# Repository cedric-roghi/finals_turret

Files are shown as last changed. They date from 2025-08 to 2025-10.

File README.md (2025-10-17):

# finals_turret
A project for the hardware and software of a simple turret replica from the greatest game show on earth, The Finals.

## Table of Contents
- [Requirements](#requirements)
- [Rationale](#rationale)
- [Installation](#installation)
- [Usage](#usage)
- [Features](#features)
- [Future_Additions](#future_additions)
- [Configuration](#configuration)
- [Known_Issues](#known_issues)

## Requirements
- Software:
    - Freecad (for 3D part design)
    - KICAD (PCB design)
    - ST Cube IDE (ST account required for download)
- Hardware:
    - BOM to come
    - Access to a 3D printer

## Rationale
- STM32f411:
    - This is a pretty overkill MCU for a project such as this. It even features I2S protocol which would make it possible for me to replace the dfplayer mini module with my own custom on board audio amplifier. The whole reason to go with this 100MHz MCU is because I want to use it for a drone project so I am testing if it works as expected first with this project. It also makes things faster for the drone project if I can copy and paste the schematic.

## Installation
No code to show yet.

Current Turret design is not great and I should have designed it in pieces to be assembled. Too much support material is needed and its hard to remove without breaking the parts.

Here is the original model from the finals that the project is based on.
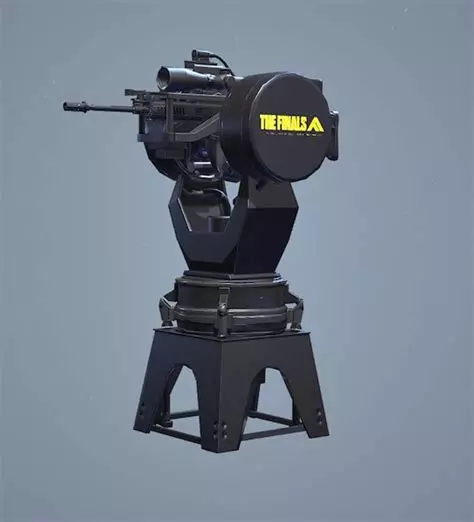
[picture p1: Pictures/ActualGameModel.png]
Game Model Its Designed After


And here is my design made in Freecad.
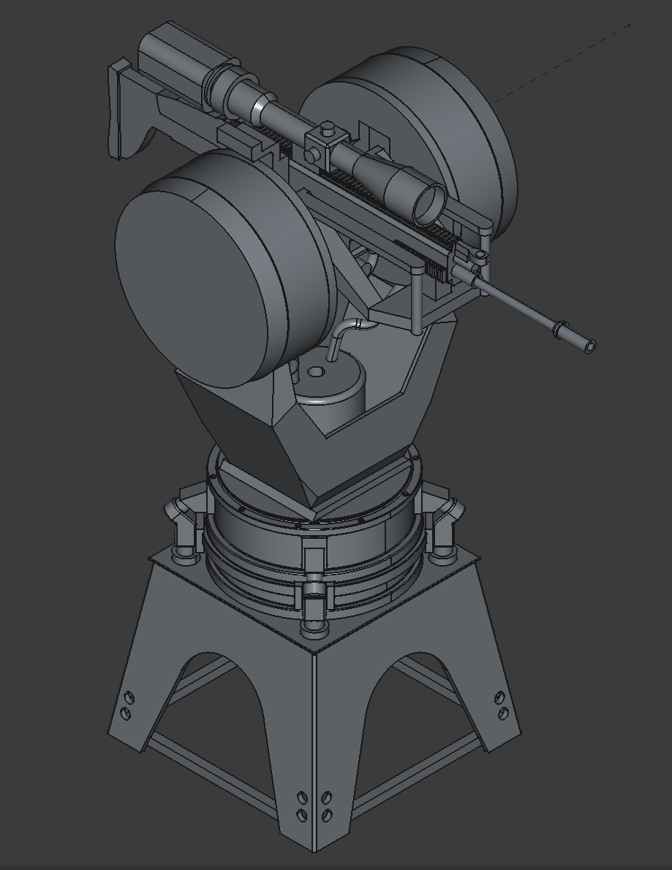
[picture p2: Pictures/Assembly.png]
Turret Assembly


Its not yet optimized for 3D printing but I believe its possible to make small changes to reduce the amount of support without affecting the looks.

FInally here is the brains of the project.
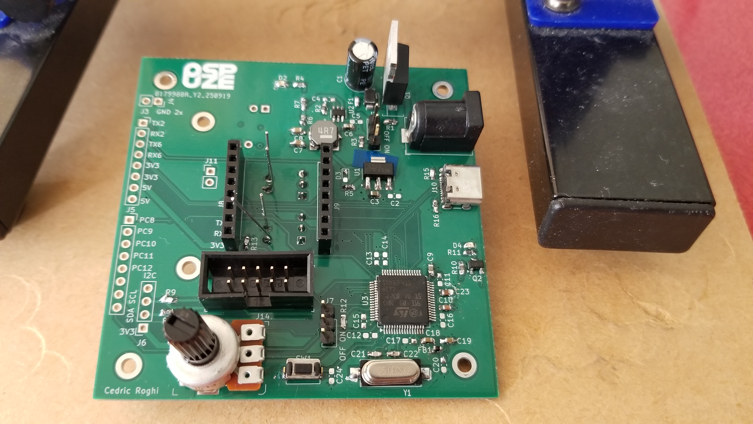
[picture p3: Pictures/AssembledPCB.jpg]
PCB


I assembled this PCB by hand using a soldering iron but I would recommend using assembly services from a manufacturer like JLCPCB. Dont forget to use a generous amount of flux if soldering the stm32 by hand.

This is how the PCB should fit into the turret. The whole thing uses M2.5 5mm screws for the speaker mounting and PCB mounting.
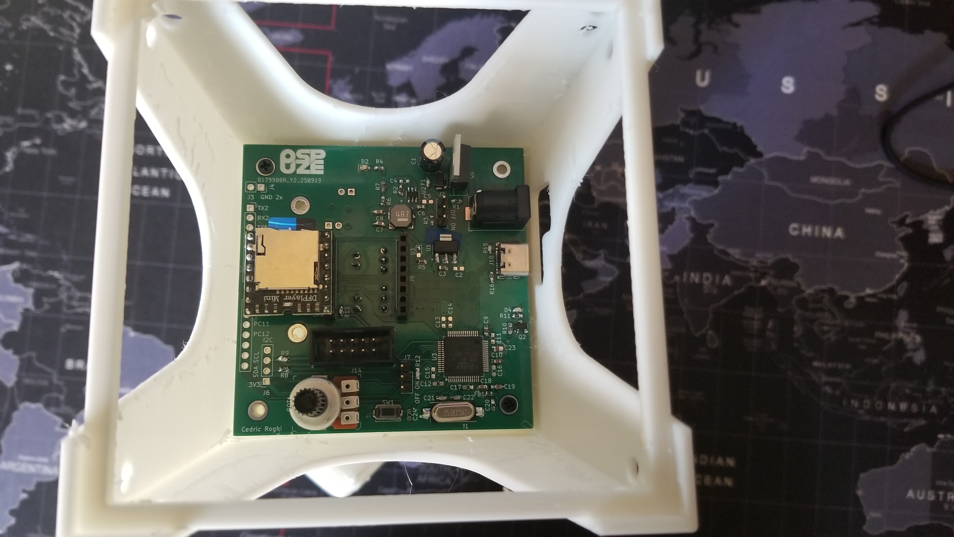
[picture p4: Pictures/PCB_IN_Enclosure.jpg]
PCB in enclosure


The servos mounting positions have mounting holes that should work with the self tapping mounting screws that are usually provided with 9g servos. The servo should be oriented so that the output rotation is in the same axis as the center of rotation for the pan and tilt respectively.

## Usage

## Features
- Audio playback using a dfplayer mini
- Programmable using SWD or USB
- USB serial communications for debugging or remote control
- USB C (2.0)
- Power input 5-12V (can use a normal 12V router power cable)
- Reverse polarity protection
- Buck converter from input stepped down to 5V for efficiency.
- Two PWM output ports to control servo motors.
- Lots of extra exposed MCU pins for rework or future quick additions.
- Potentiometer for volume control

## Future_Additions
- Raspberry pi python code for tracking people with a camera
- New and improved PCB with its own on board audio amplifier + SD card slot or some other form of audio storage

## Configuration

## Known Issues
- The standoff for the dfplayer mini is the wrong way around.
- The port for the USB and barrel jack connector should be at the back and not the side.
- The 3.3V LDO large pin is in fact connected to Vout and not GND. I need to fix the footprint in KiCAD.

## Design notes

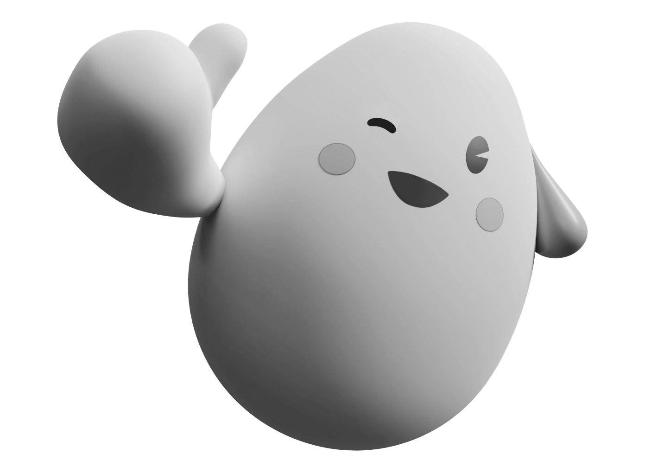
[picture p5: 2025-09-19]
Pictures/namatamagreyscale.png

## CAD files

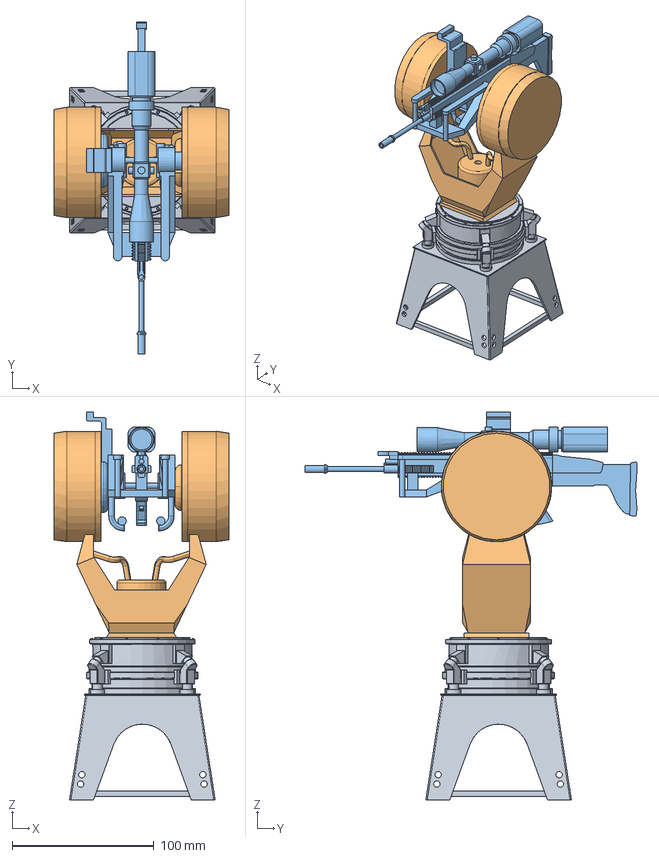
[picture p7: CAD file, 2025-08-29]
3D Assembly/TheFinalsTurretAssembly.FCStd
123.5 x 234.9 x 274.2 mm
FinalsTurretBase_V2_001
FinalsTurretTop_001
turretShooter_001
Servo TowerPro 9g SG90
Servo TowerPro 9g SG091

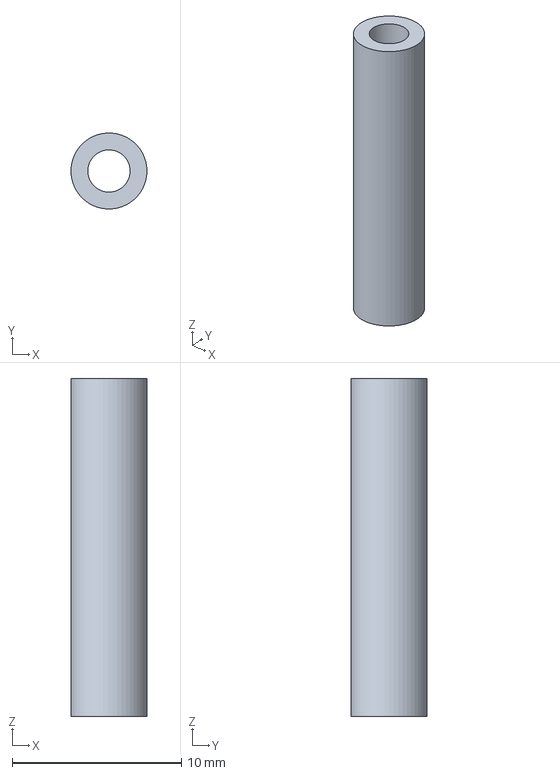
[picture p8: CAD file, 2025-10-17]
3D Assembly/SpeakerStandoffs.FCStd
4.50 x 4.50 x 20.0 mm

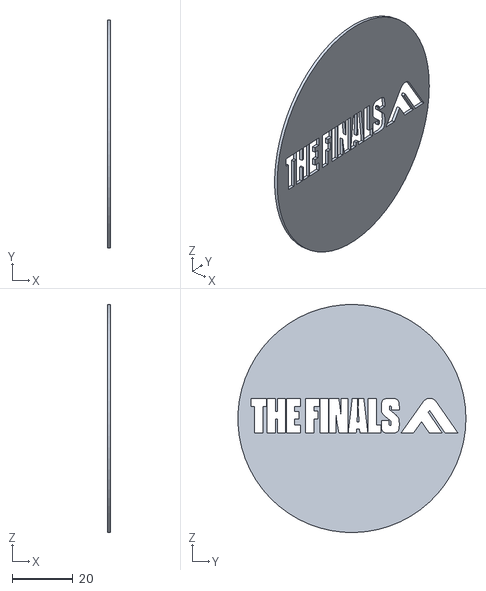
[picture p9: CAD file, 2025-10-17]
3D Assembly/STL_FILES/FinalsTurretTop-LogoStencil.stl
1.00 x 75.3 x 75.3

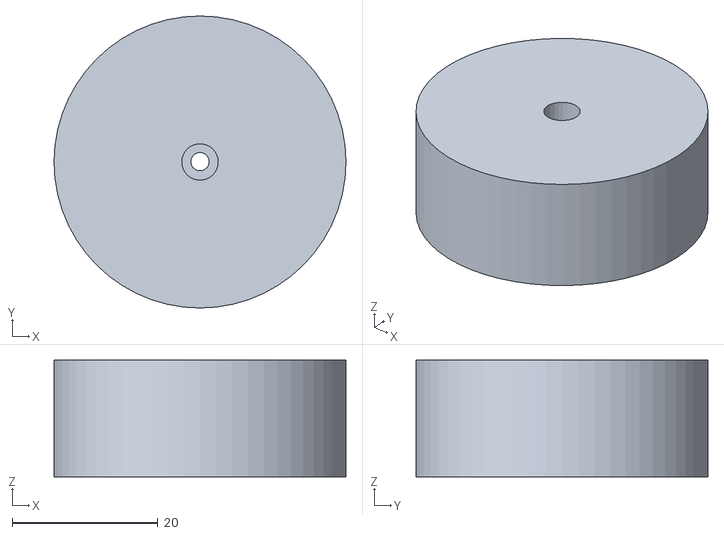
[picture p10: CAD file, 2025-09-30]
3D Assembly/STL_FILES/FinalsTurretTop-ServoArmFitTest.stl
40.0 x 40.0 x 16.0

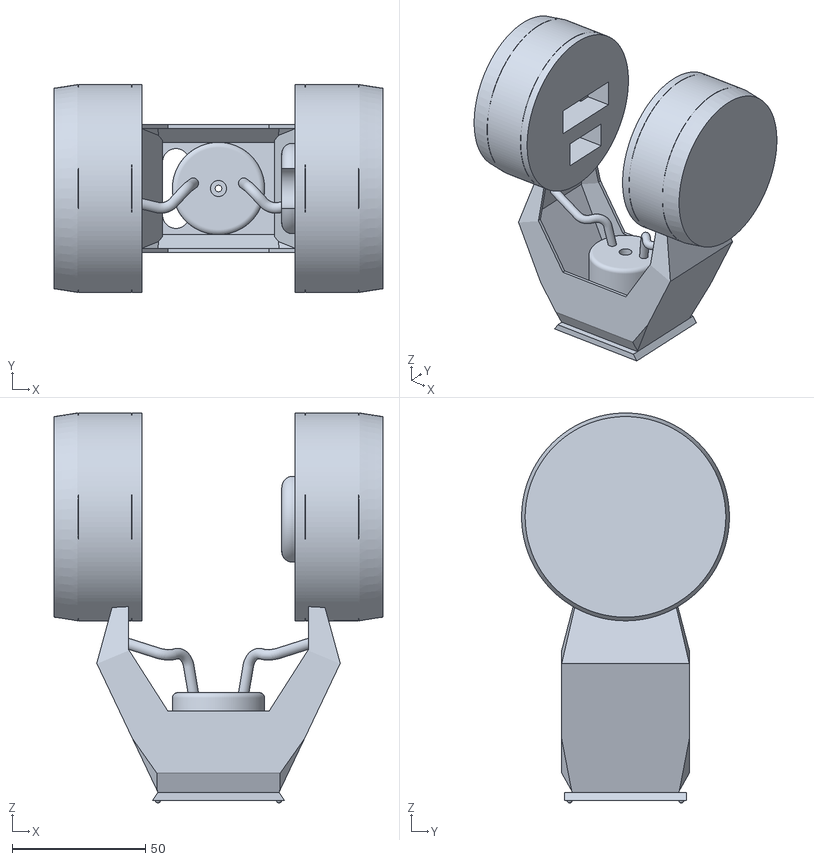
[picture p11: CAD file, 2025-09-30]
3D Assembly/STL_FILES/FinalsTurretTop-Body.stl
123.5 x 78.1 x 146.6

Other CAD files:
3D Assembly/STL_FILES/SpeakerStandoffs-Body.stl

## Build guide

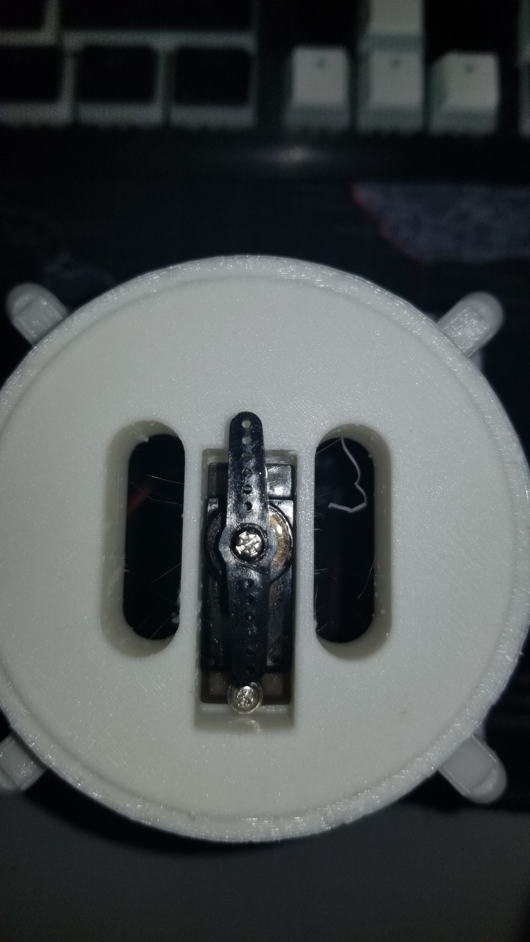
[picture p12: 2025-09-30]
3D Assembly/servoarmreference.jpg

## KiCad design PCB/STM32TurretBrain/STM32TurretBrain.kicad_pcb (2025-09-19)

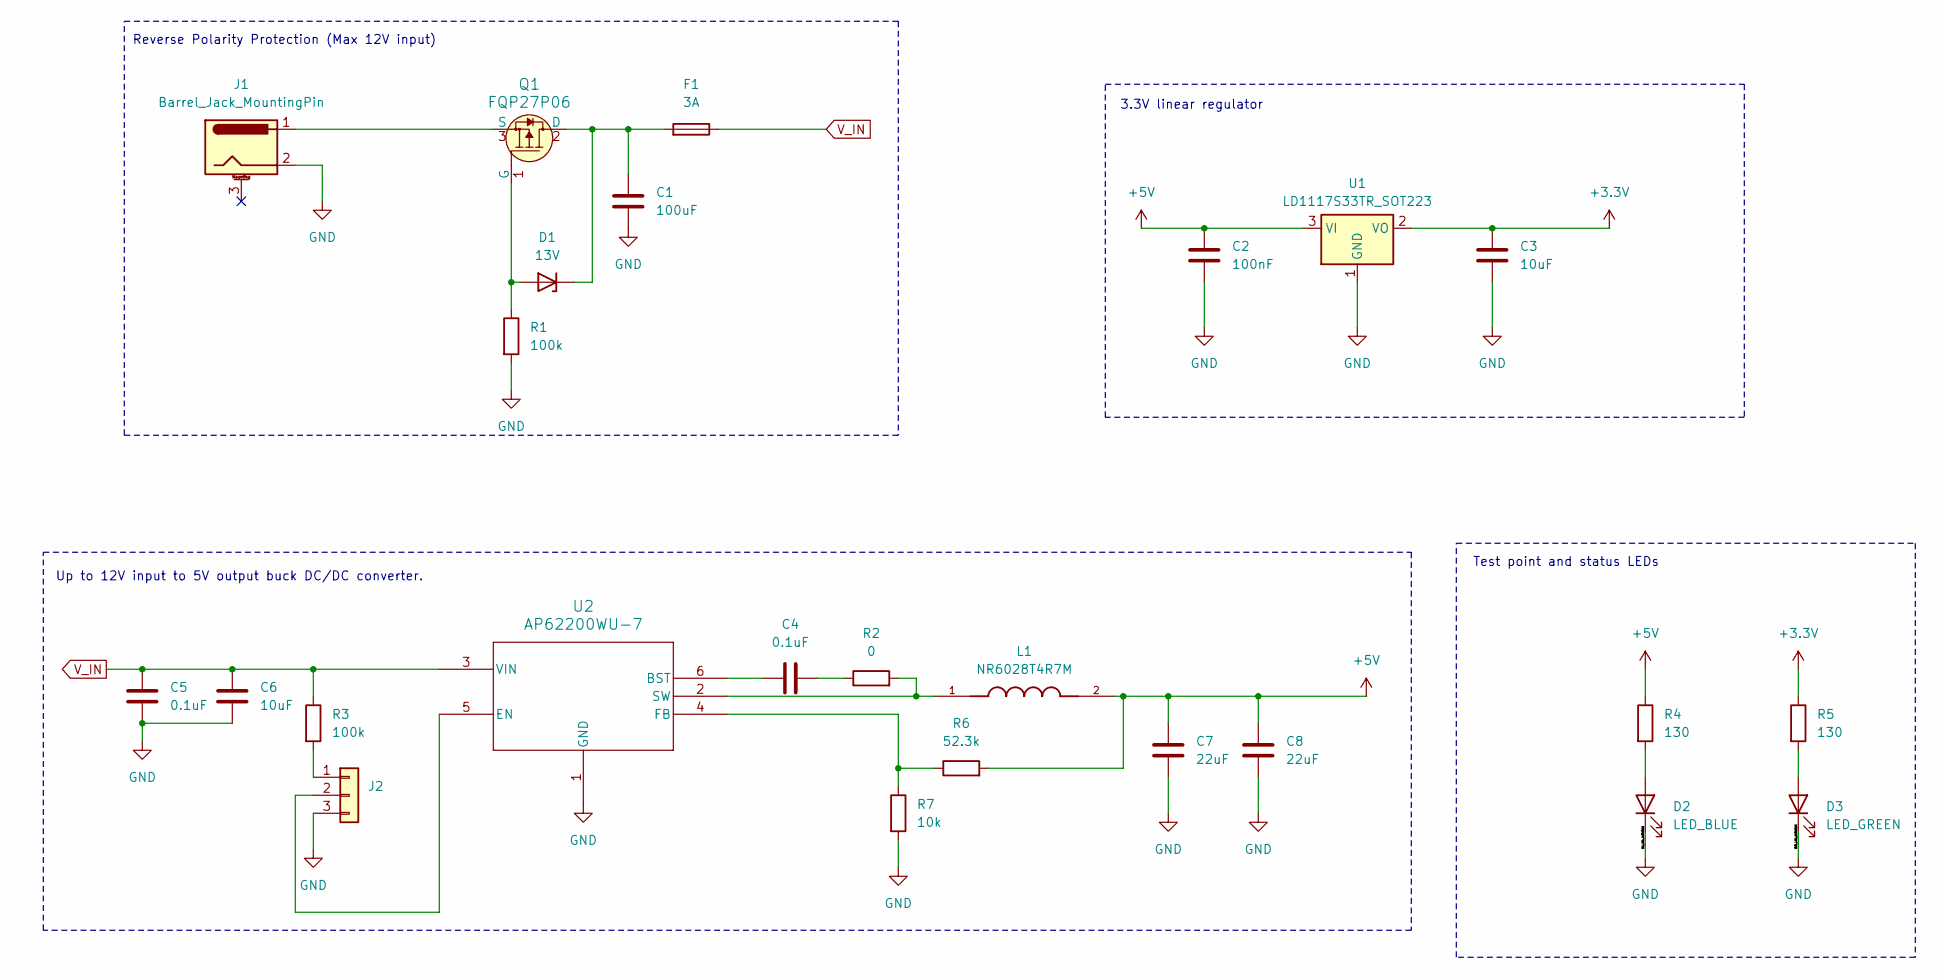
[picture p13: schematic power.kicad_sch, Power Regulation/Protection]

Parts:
C1: 100uF; C_Radial_D6.3mm_H5.0mm_P2.50mm
C2: 100nF; C_0603_1608Metric_Pad1.08x0.95mm_HandSolder
C3, C6: 10uF; C_0603_1608Metric_Pad1.08x0.95mm_HandSolder
C4, C5: 0.1uF; C_0603_1608Metric_Pad1.08x0.95mm_HandSolder
C7, C8: 22uF; C_0603_1608Metric_Pad1.08x0.95mm_HandSolder
D1: 13V; Nexperia_CFP3_SOD-123W
D2: LED_BLUE; LED_0603_1608Metric_Pad1.05x0.95mm_HandSolder
D3: LED_GREEN; LED_0603_1608Metric_Pad1.05x0.95mm_HandSolder
F1: 3A; Fuse_0603_1608Metric_Pad1.05x0.95mm_HandSolder
J1: Barrel_Jack_MountingPin; BarrelJack_Horizontal
J2: Conn_01x03; PinHeader_1x03_P2.54mm_Vertical
L1: NR6028T4R7M; IND_NR6028T4R7M
Q1: FQP27P06; TO-220-3; MPN FQP27P06; Digi-Key_PN FQP27P06-ND
R1, R3: 100k; R_0603_1608Metric_Pad0.98x0.95mm_HandSolder
R2: 0; R_0603_1608Metric_Pad0.98x0.95mm_HandSolder
R4, R5: 130; R_0603_1608Metric_Pad0.98x0.95mm_HandSolder
R6: 52.3k; R_0603_1608Metric_Pad0.98x0.95mm_HandSolder
R7: 10k; R_0603_1608Metric_Pad0.98x0.95mm_HandSolder
U1: LD1117S33TR_SOT223; SOT-223
U2: AP62200WU-7; TSOT26-WU_DIO-M

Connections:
+3.3V: C3.1, R5.1, U1.2 (VO); also elsewhere on the board
+5V: C2.1, C7.1, C8.1, L1.2, R4.1, R6.2, U1.3 (VI); also elsewhere on the board
GND: C1.2, C2.2, C3.2, C5.2, C6.2, C7.2, C8.2, D2.1 (K), D3.1 (K), J1.2, J2.3, R1.2, R7.2, U1.1 (GND), U2.1 (GND); also elsewhere on the board
unnamed: C4.2, R2.1
unnamed: D1.2 (A), Q1.1 (G), R1.1
unnamed: C1.1, D1.1 (K), F1.2, Q1.2 (D)
unnamed: D2.2 (A), R4.2
unnamed: D3.2 (A), R5.2
unnamed: J2.1, R3.2
unnamed: J2.2, U2.5 (EN)
unnamed: J1.1, Q1.3 (S)
unnamed: C4.1, U2.6 (BST)
unnamed: R6.1, R7.1, U2.4 (FB)
unnamed: L1.1, R2.2, U2.2 (SW)
V_IN: C5.1, C6.1, F1.1, R3.1, U2.3 (VIN)

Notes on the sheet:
Up to 12V input to 5V output buck DC/DC converter.
3.3V linear regulator
Test point and status LEDs
Reverse Polarity Protection (Max 12V input)

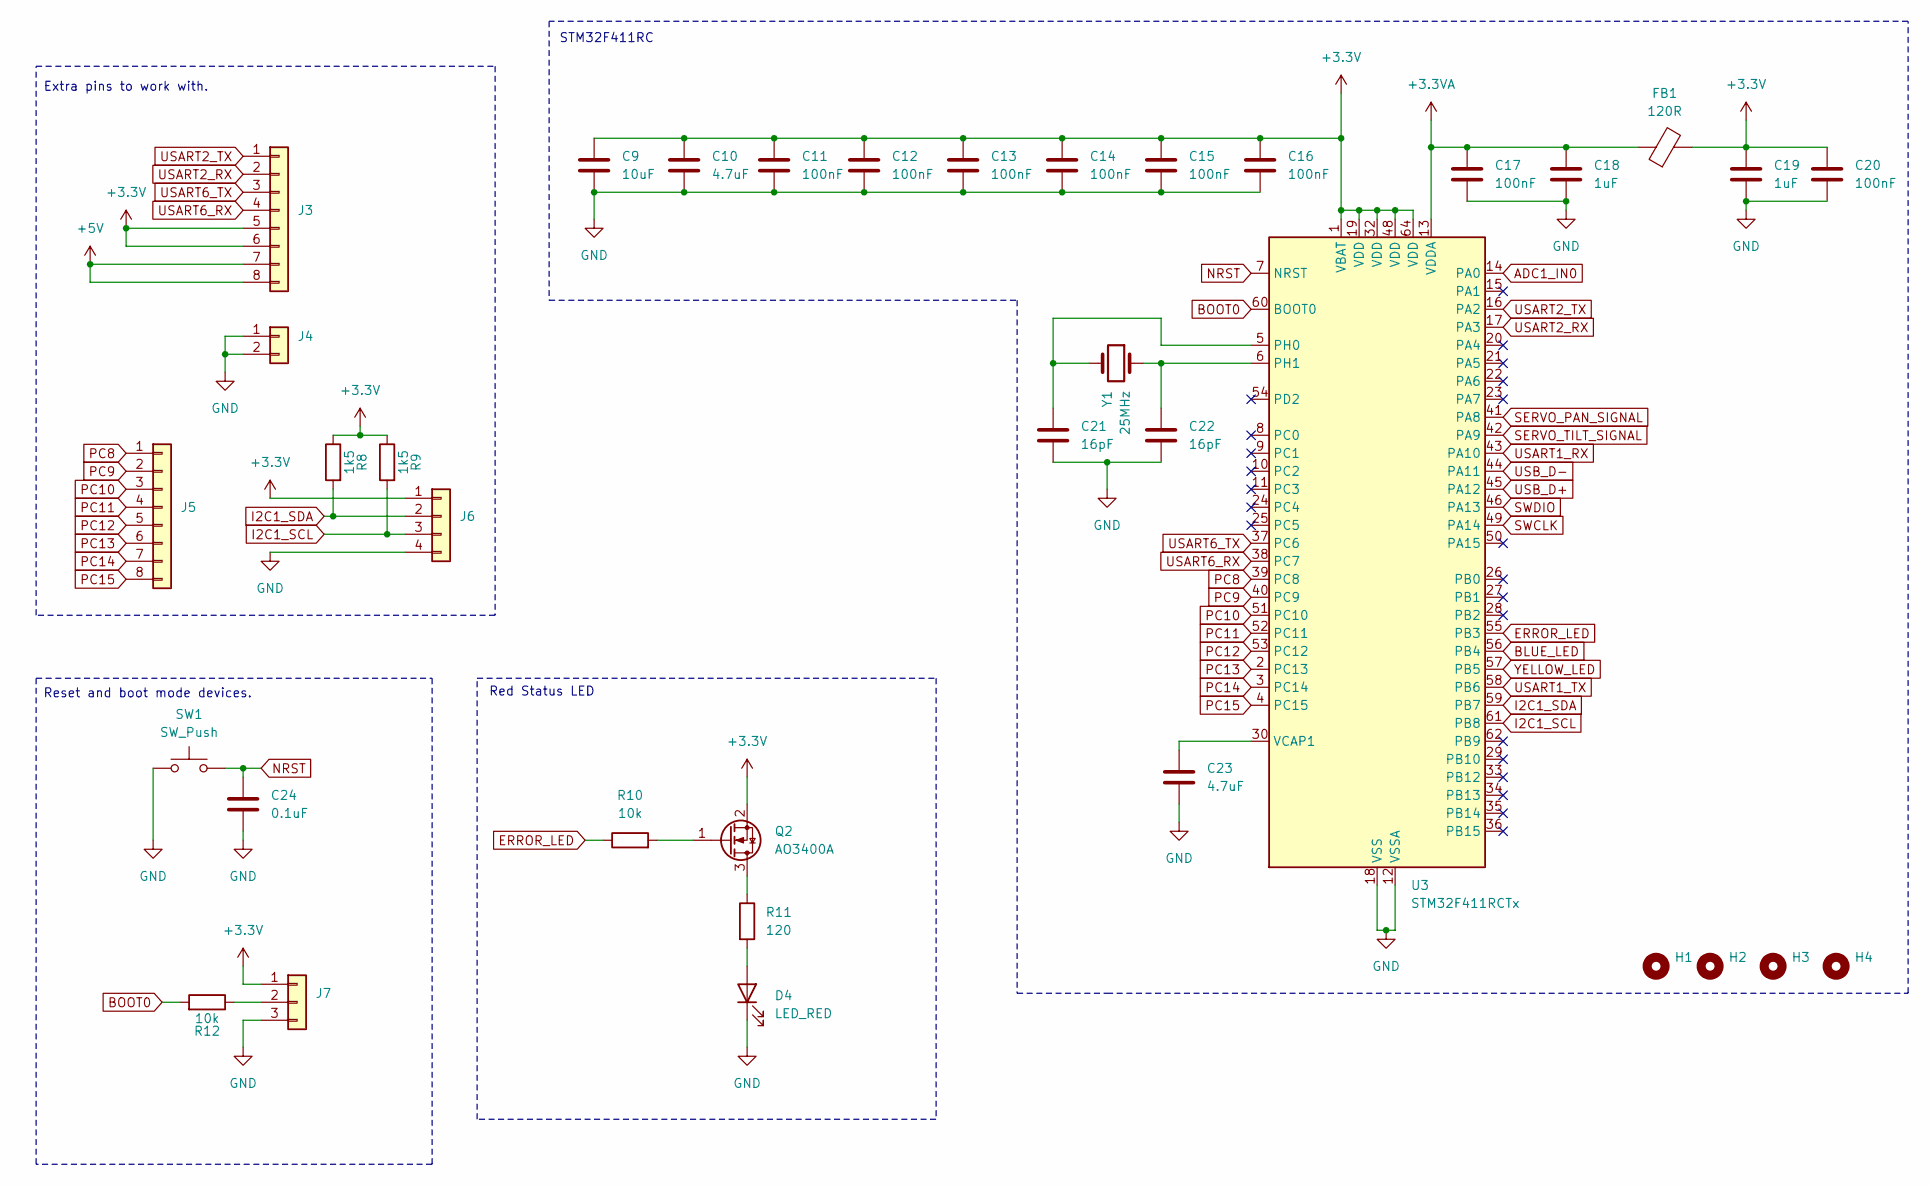
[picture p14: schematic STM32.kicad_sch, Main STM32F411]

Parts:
C9: 10uF; C_0603_1608Metric_Pad1.08x0.95mm_HandSolder
C10, C23: 4.7uF; C_0603_1608Metric_Pad1.08x0.95mm_HandSolder
C11, C12, C13, C14, C15, C16, C17, C20: 100nF; C_0603_1608Metric_Pad1.08x0.95mm_HandSolder
C18, C19: 1uF; C_0603_1608Metric_Pad1.08x0.95mm_HandSolder
C21, C22: 16pF; C_0603_1608Metric_Pad1.08x0.95mm_HandSolder
C24: 0.1uF; C_0603_1608Metric_Pad1.08x0.95mm_HandSolder
D4: LED_RED; LED_0603
FB1: 120R; 0603
H1, H2, H3, H4: MountingHole; MountingHole_2.7mm_M2.5_DIN965_Pad
J3, J5: Conn_01x08; PinSocket_1x08_P2.54mm_Vertical
J4: Conn_01x02; PinSocket_1x02_P2.54mm_Vertical
J6: Conn_01x04; PinSocket_1x04_P2.54mm_Vertical
J7: Conn_01x03; PinHeader_1x03_P2.54mm_Vertical
Q2: AO3400A; SOT-23
R8, R9: 1k5; R_0603_1608Metric_Pad0.98x0.95mm_HandSolder
R10, R12: 10k; R_0603_1608Metric_Pad0.98x0.95mm_HandSolder
R11: 120; R_0603_1608Metric_Pad0.98x0.95mm_HandSolder
SW1: SW_Push; SW_SPST_EVQPE1
U3: STM32F411RCTx; LQFP-64_10x10mm_P0.5mm
Y1: 25MHz; XTAL_ECS-250-18-5PX-F-TR

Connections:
+3.3V: C9.1, C10.1, C11.1, C12.1, C13.1, C14.1, C15.1, C16.1, C19.1, C20.1, FB1.2, J3.5, J3.6, J6.1, J7.1, Q2.2 (S), R8.1, R9.1, U3.1 (VBAT), U3.19 (VDD), U3.32 (VDD), U3.48 (VDD), U3.64 (VDD); also elsewhere on the board
+3.3VA: C17.1, C18.1, FB1.1, U3.13 (VDDA)
+5V: J3.7, J3.8; also elsewhere on the board
ADC1_IN0: U3.14 (PA0); also elsewhere on the board
BLUE_LED: U3.56 (PB4); also elsewhere on the board
BOOT0: R12.2, U3.60 (BOOT0)
ERROR_LED: R10.1, U3.55 (PB3)
GND: C9.2, C10.2, C11.2, C12.2, C13.2, C14.2, C15.2, C16.2, C17.2, C18.2, C19.2, C20.2, C21.2, C22.2, C23.2, C24.2, D4.1 (K), J4.1, J4.2, J6.4, J7.3, SW1.1, U3.12 (VSSA), U3.18 (VSS), U3.31 (VSS), U3.47 (VSS), U3.63 (VSS); also elsewhere on the board
I2C1_SCL: J6.3, R9.2, U3.61 (PB8)
I2C1_SDA: J6.2, R8.2, U3.59 (PB7)
NRST: C24.1, SW1.2, U3.7 (NRST)
unnamed: D4.2 (A), R11.2
unnamed: J7.2, R12.1
unnamed: Q2.3 (D), R11.1
unnamed: Q2.1 (G), R10.2
unnamed: C21.1, U3.5 (PH0), Y1.2
unnamed: C22.1, U3.6 (PH1), Y1.1
unnamed: C23.1, U3.30 (VCAP1)
PC8: J5.1, U3.39 (PC8)
PC9: J5.2, U3.40 (PC9)
PC10: J5.3, U3.51 (PC10)
PC11: J5.4, U3.52 (PC11)
PC12: J5.5, U3.53 (PC12)
PC13: J5.6, U3.2 (PC13)
PC14: J5.7, U3.3 (PC14)
PC15: J5.8, U3.4 (PC15)
SERVO_PAN_SIGNAL: U3.41 (PA8); also elsewhere on the board
SERVO_TILT_SIGNAL: U3.42 (PA9); also elsewhere on the board
SWCLK: U3.49 (PA14); also elsewhere on the board
SWDIO: U3.46 (PA13); also elsewhere on the board
USART1_RX: U3.43 (PA10); also elsewhere on the board
USART1_TX: U3.58 (PB6); also elsewhere on the board
USART2_RX: J3.2, U3.17 (PA3)
USART2_TX: J3.1, U3.16 (PA2)
USART6_RX: J3.4, U3.38 (PC7)
USART6_TX: J3.3, U3.37 (PC6)
USB_D+: U3.45 (PA12); also elsewhere on the board
USB_D-: U3.44 (PA11); also elsewhere on the board
YELLOW_LED: U3.57 (PB5); also elsewhere on the board

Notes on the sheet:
Extra pins to work with.
Red Status LED
STM32F411RC
Reset and boot mode devices.

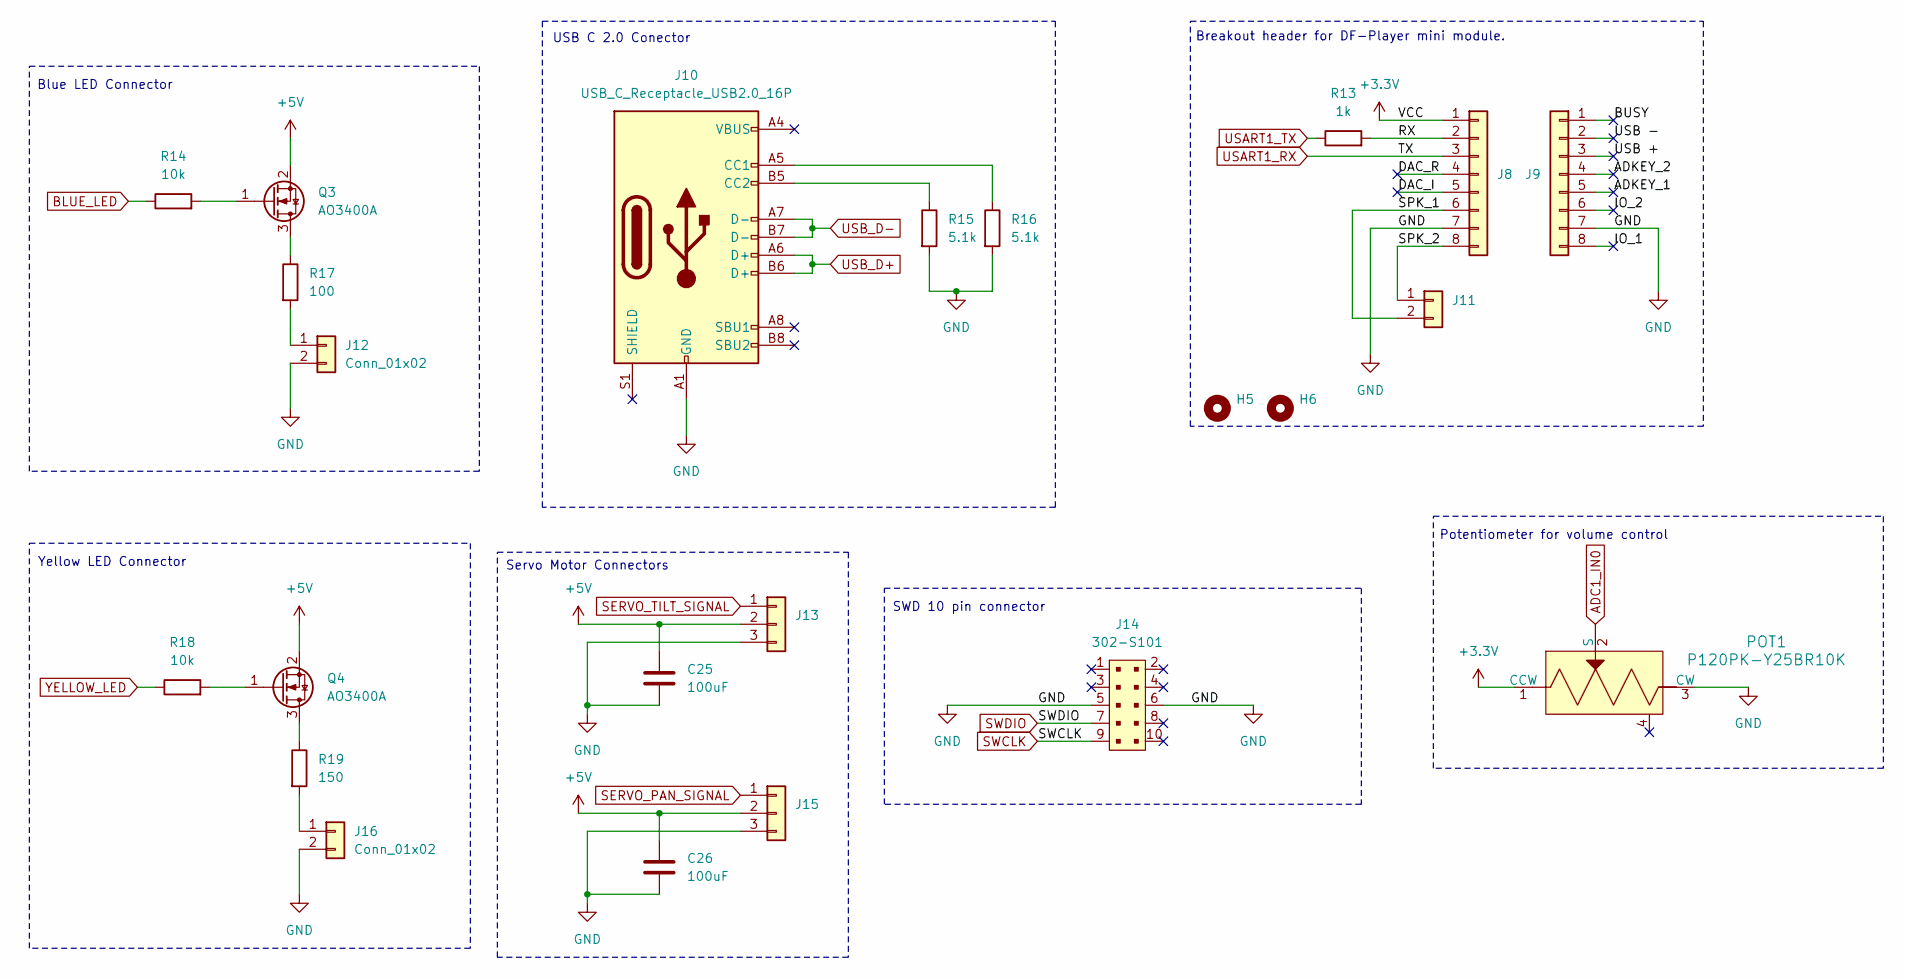
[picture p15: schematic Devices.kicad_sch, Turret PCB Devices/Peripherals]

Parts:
C25, C26: 100uF; C_Radial_D6.3mm_H5.0mm_P2.50mm
H5, H6: MountingHole; MountingHole_2.7mm_M2.5_DIN965_Pad
J8, J9: Conn_01x08; PinHeader_1x08_P2.54mm_Vertical
J10: USB_C_Receptacle_USB2.0_16P; USB_C_Receptacle_GCT_USB4105-xx-A_16P_TopMnt_Horizontal
J11: Conn_01x02; PinHeader_1x02_P2.54mm_Vertical
J12, J16: Conn_01x02; PinSocket_1x02_P2.54mm_Vertical
J13, J15: Conn_01x03; PinHeader_1x03_P2.54mm_Vertical
J14: 302-S101; PinHeader_2x5_P2.54mm_Drill1.2mm; MPN 302-S101; Digi-Key_PN ED1543-ND
POT1: P120PK-Y25BR10K; Potentiometer_P120PK-Y25BR10K; MPN P120PK-Y25BR10K; Digi-Key_PN 987-1710-ND
Q3, Q4: AO3400A; SOT-23
R13: 1k; R_0603_1608Metric_Pad0.98x0.95mm_HandSolder
R14, R18: 10k; R_0603_1608Metric_Pad0.98x0.95mm_HandSolder
R15, R16: 5.1k; R_0603_1608Metric_Pad0.98x0.95mm_HandSolder
R17: 100; R_0603_1608Metric_Pad0.98x0.95mm_HandSolder
R19: 150; R_0603_1608Metric_Pad0.98x0.95mm_HandSolder

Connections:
+3.3V: J8.1, POT1.1 (CCW); also elsewhere on the board
+5V: C25.1, C26.1, J13.2, J15.2, Q3.2 (S), Q4.2 (S); also elsewhere on the board
/Devices/ADKEY_1: J9.5
/Devices/ADKEY_2: J9.4
/Devices/BUSY: J9.1
/Devices/DAC_I: J8.5
/Devices/DAC_R: J8.4
/Devices/IO_1: J9.8
/Devices/IO_2: J9.6
/Devices/RX: J8.2, R13.2
/Devices/SPK_1: J8.6, J11.2
/Devices/SPK_2: J8.8, J11.1
/Devices/USB +: J9.3
/Devices/USB -: J9.2
ADC1_IN0: POT1.2 (S); also elsewhere on the board
BLUE_LED: R14.1; also elsewhere on the board
GND: C25.2, C26.2, J8.7, J9.7, J10.A1 (GND), J10.A12 (GND), J10.B1 (GND), J10.B12 (GND), J12.2, J13.3, J14.5, J14.6, J15.3, J16.2, POT1.3 (CW), R15.2, R16.2; also elsewhere on the board
unnamed: J10.A5 (CC1), R16.1
unnamed: J10.B5 (CC2), R15.1
unnamed: J12.1, R17.2
unnamed: J16.1, R19.2
unnamed: Q3.3 (D), R17.1
unnamed: Q3.1 (G), R14.2
unnamed: Q4.3 (D), R19.1
unnamed: Q4.1 (G), R18.2
SERVO_PAN_SIGNAL: J15.1; also elsewhere on the board
SERVO_TILT_SIGNAL: J13.1; also elsewhere on the board
SWCLK: J14.9; also elsewhere on the board
SWDIO: J14.7; also elsewhere on the board
USART1_RX: J8.3; also elsewhere on the board
USART1_TX: R13.1; also elsewhere on the board
USB_D+: J10.A6 (D+), J10.B6 (D+); also elsewhere on the board
USB_D-: J10.A7 (D-), J10.B7 (D-); also elsewhere on the board
YELLOW_LED: R18.1; also elsewhere on the board

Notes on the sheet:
Servo Motor Connectors
USB C 2.0 Conector
Blue LED Connector
Yellow LED Connector
SWD 10 pin connector
Breakout header for DF-Player mini module.
Potentiometer for volume control

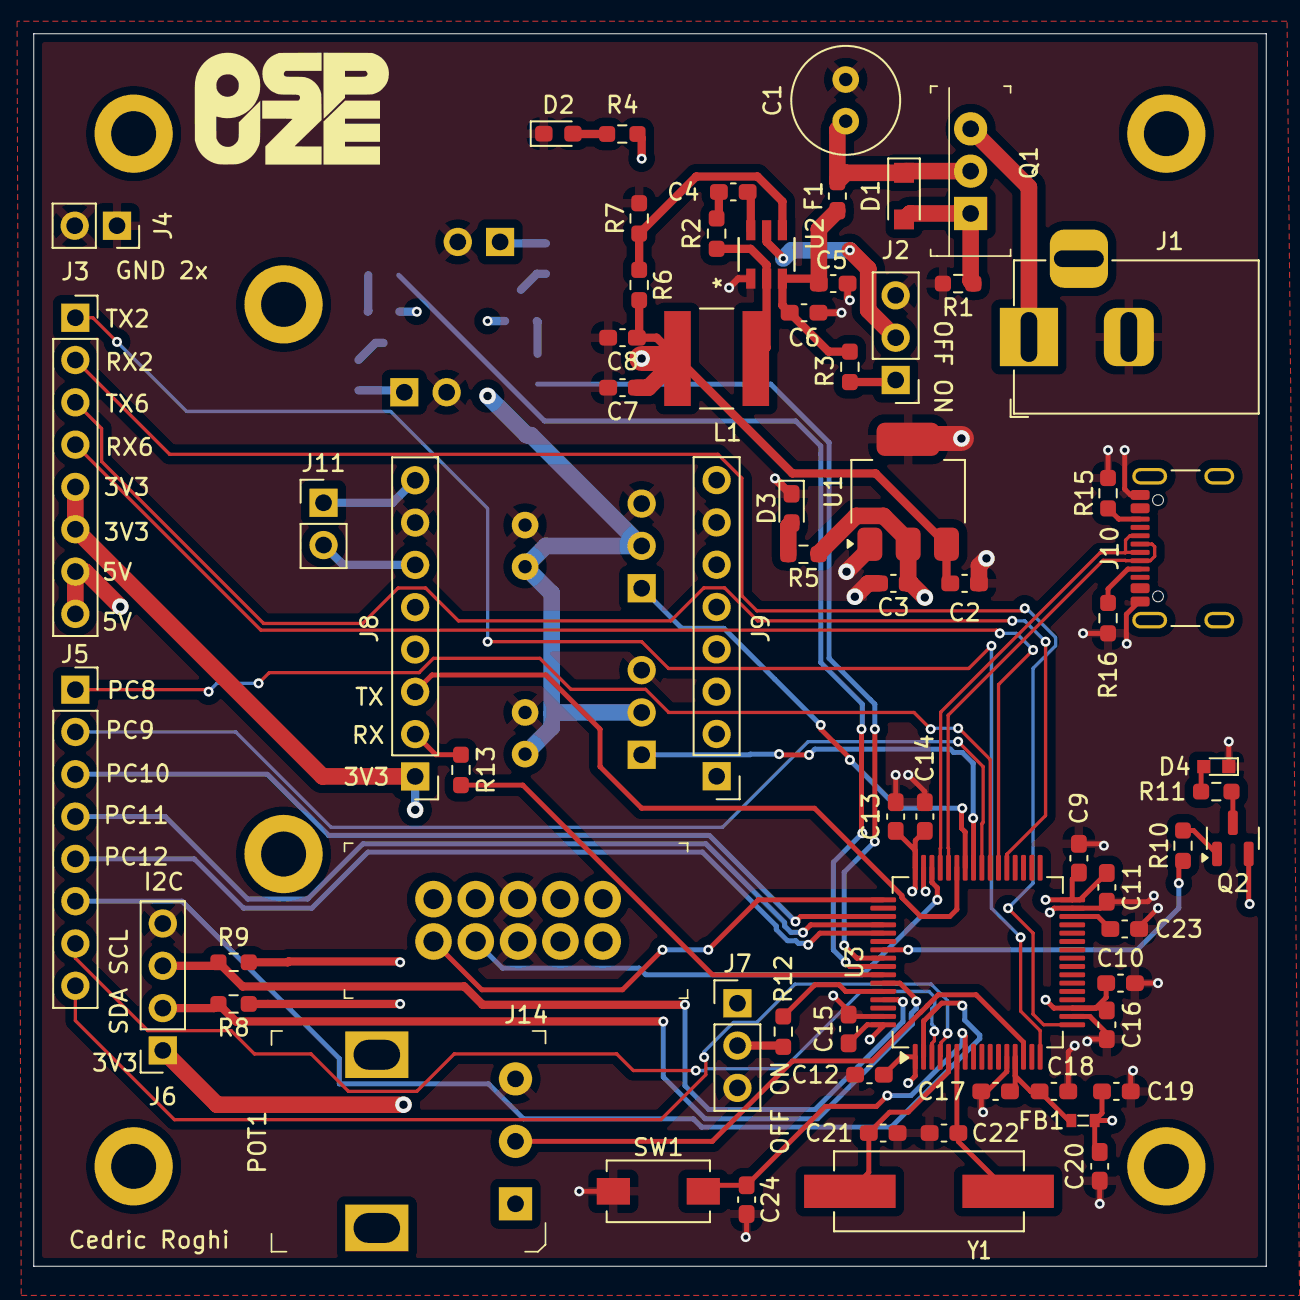
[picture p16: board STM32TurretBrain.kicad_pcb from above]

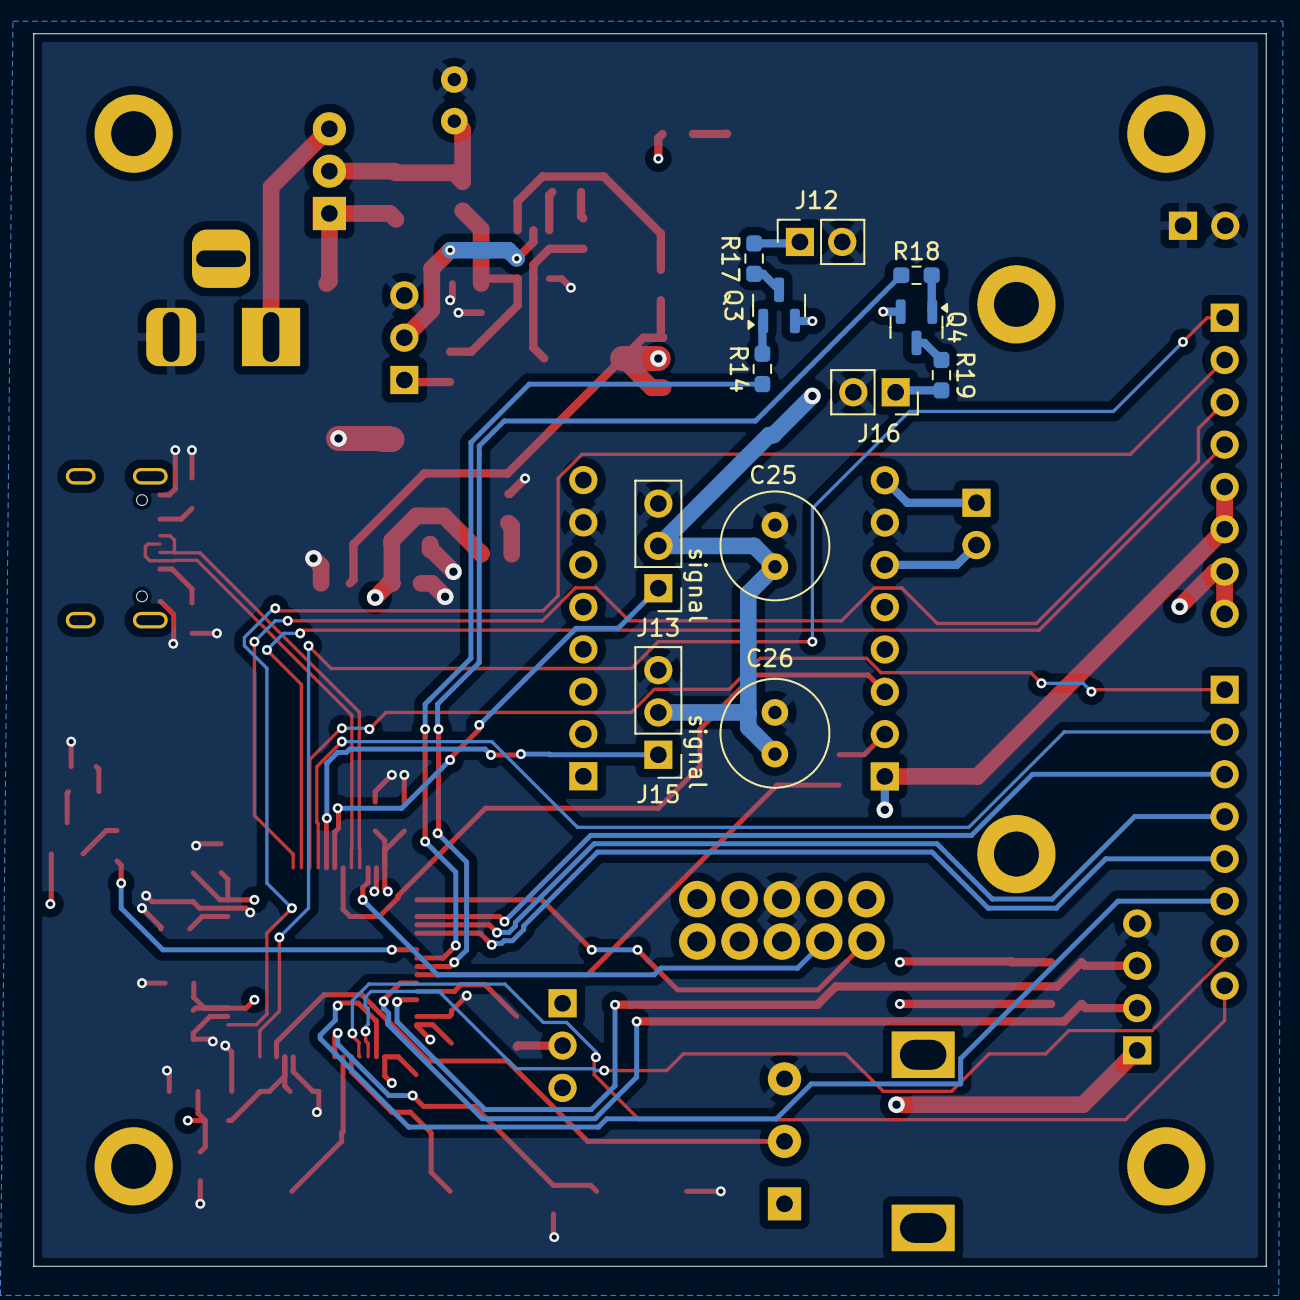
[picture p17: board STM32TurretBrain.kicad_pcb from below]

Board: 4 copper layers, 74.0 x 74.0 mm, 84 parts (12 on the bottom side), 62 nets.

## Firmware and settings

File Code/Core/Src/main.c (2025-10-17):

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
/* Includes ------------------------------------------------------------------*/
#include "main.h"
#include "cmsis_os.h"

ADC_HandleTypeDef hadc1;

TIM_HandleTypeDef htim1;

UART_HandleTypeDef huart1;

PCD_HandleTypeDef hpcd_USB_OTG_FS;

/* Definitions for defaultTask */
osThreadId_t defaultTaskHandle;
const osThreadAttr_t defaultTask_attributes = {
  .name = "defaultTask",
  .stack_size = 128 * 4,
  .priority = (osPriority_t) osPriorityNormal,
};
void SystemClock_Config(void);
static void MX_GPIO_Init(void);
static void MX_TIM1_Init(void);
static void MX_USART1_UART_Init(void);
static void MX_USB_OTG_FS_PCD_Init(void);
static void MX_ADC1_Init(void);
void StartDefaultTask(void *argument);

/**
  * @brief  The application entry point.
  * @retval int
  */
int main(void)
{

  /* MCU Configuration--------------------------------------------------------*/

  /* Reset of all peripherals, Initializes the Flash interface and the Systick. */
  HAL_Init();

  /* Configure the system clock */
  SystemClock_Config();

  /* Initialize all configured peripherals */
  MX_GPIO_Init();
  MX_TIM1_Init();
  MX_USART1_UART_Init();
  MX_USB_OTG_FS_PCD_Init();
  MX_ADC1_Init();
  /* USER CODE BEGIN 2 */
  HAL_TIM_PWM_Start(&htim1, TIM_CHANNEL_1);
  /* USER CODE END 2 */

  /* Init scheduler */
  osKernelInitialize();

  /* USER CODE BEGIN RTOS_MUTEX */
  /* add mutexes, ... */
  /* USER CODE END RTOS_MUTEX */

  /* USER CODE BEGIN RTOS_SEMAPHORES */
  /* add semaphores, ... */
  /* USER CODE END RTOS_SEMAPHORES */

  /* USER CODE BEGIN RTOS_TIMERS */
  /* start timers, add new ones, ... */
  /* USER CODE END RTOS_TIMERS */

  /* USER CODE BEGIN RTOS_QUEUES */
  /* add queues, ... */
  /* USER CODE END RTOS_QUEUES */

  /* Create the thread(s) */
  /* creation of defaultTask */
  defaultTaskHandle = osThreadNew(StartDefaultTask, NULL, &defaultTask_attributes);

  /* USER CODE BEGIN RTOS_THREADS */
  /* add threads, ... */
  /* USER CODE END RTOS_THREADS */

  /* USER CODE BEGIN RTOS_EVENTS */
  /* add events, ... */
  /* USER CODE END RTOS_EVENTS */

  /* Start scheduler */
  osKernelStart();

  /* We should never get here as control is now taken by the scheduler */

  /* Infinite loop */
  /* USER CODE BEGIN WHILE */
  while (1)
  {
    /* USER CODE END WHILE */

    /* USER CODE BEGIN 3 */
  }
  /* USER CODE END 3 */
}

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
/* USER CODE BEGIN 4 */
static uint32_t AngleToCCR(uint16_t angle)
{
    const uint32_t MIN_PULSE_US = 500;   // 1 ms
    const uint32_t MAX_PULSE_US = 2500;   // 2 ms

    if (angle > 180U) angle = 180U;        // clamp

    return MIN_PULSE_US +
           ((MAX_PULSE_US - MIN_PULSE_US) * angle) / 180U;
}

void Pan_Servo_SetAngle(uint16_t angle)
{
    __HAL_TIM_SET_COMPARE(&htim1, TIM_CHANNEL_1, AngleToCCR(angle));
}

static uint16_t ADC_Value_To_Angle(uint32_t adc_val)
{
    /* Clamp just in case */
    if (adc_val > 4095U) adc_val = 4095U;

    /* Linear mapping: 0 → 0°, 4095 → 180° */
    return (uint16_t)((adc_val * 180U) / 4095U);
}
/* USER CODE END 4 */

/* USER CODE BEGIN Header_StartDefaultTask */
/**
  * @brief  Function implementing the defaultTask thread.
  * @param  argument: Not used
  * @retval None
  */
/* USER CODE END Header_StartDefaultTask */
void StartDefaultTask(void *argument)
{
  /* USER CODE BEGIN 5 */
  /* Infinite loop */
	while (1)
	{
		uint32_t adc_raw = 0;

		/* ---- 1. Trigger a single conversion -------------------------------- */
		HAL_ADC_Start(&hadc1);                     // start conversion
		if (HAL_ADC_PollForConversion(&hadc1, 10) == HAL_OK)   // timeout = 10 ms
		{
			adc_raw = HAL_ADC_GetValue(&hadc1);    // 0 … 4095
		}
		HAL_ADC_Stop(&hadc1);                      // stop (optional, saves power)

		/* ---- 2. Convert ADC → angle --------------------------------------- */
		uint16_t angle = ADC_Value_To_Angle(adc_raw);

		/* ---- 3. Convert angle → CCR and write it --------------------------- */
		uint32_t ccr = AngleToCCR(angle);
		__HAL_TIM_SET_COMPARE(&htim1, TIM_CHANNEL_1, ccr);

		/* ---- 4. Small delay – you can tune this to taste ----------------- */
		osDelay(20);      // 20 ms ≈ one PWM period; feel free to increase
	}
  /* USER CODE END 5 */
}

/**
  * @brief  Period elapsed callback in non blocking mode
  * @note   This function is called  when TIM2 interrupt took place, inside
  * HAL_TIM_IRQHandler(). It makes a direct call to HAL_IncTick() to increment
  * a global variable "uwTick" used as application time base.
  * @param  htim : TIM handle
  * @retval None
  */
void HAL_TIM_PeriodElapsedCallback(TIM_HandleTypeDef *htim)
{
  if (htim->Instance == TIM2)
  {
    HAL_IncTick();
  }
}

/**
  * @brief  This function is executed in case of error occurrence.
  * @retval None
  */
void Error_Handler(void)
{
  /* USER CODE BEGIN Error_Handler_Debug */
  /* User can add his own implementation to report the HAL error return state */
  __disable_irq();
  while (1)
  {
  }
  /* USER CODE END Error_Handler_Debug */
}
#ifdef USE_FULL_ASSERT
/**
  * @brief  Reports the name of the source file and the source line number
  *         where the assert_param error has occurred.
  * @param  file: pointer to the source file name
  * @param  line: assert_param error line source number
  * @retval None
  */
void assert_failed(uint8_t *file, uint32_t line)
{
  /* USER CODE BEGIN 6 */
  /* User can add his own implementation to report the file name and line number,
     ex: printf("Wrong parameters value: file %s on line %d\r\n", file, line) */
  /* USER CODE END 6 */
}
#endif /* USE_FULL_ASSERT */

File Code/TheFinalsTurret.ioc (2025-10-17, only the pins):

Mcu.UserName=STM32F411RCTx
PA0-WKUP.Signal=ADCx_IN0
PA10.Signal=USART1_RX
PA11.Signal=USB_OTG_FS_DM
PA12.Signal=USB_OTG_FS_DP
PA13.Signal=SYS_JTMS-SWDIO
PA14.Signal=SYS_JTCK-SWCLK
PA15.Signal=USART1_TX
PA8.Signal=S_TIM1_CH1
PA9.Signal=S_TIM1_CH2
PB3.Signal=GPIO_Output
PB4.Signal=GPIO_Output
PB5.Signal=GPIO_Output

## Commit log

2025-08-29 first commit with cad files
    [TheFinalsTurretAssembly.FCStd]
2025-09-19 finished PCB V1
    [Devices.kicad_sch, STM32.kicad_sch, STM32TurretBrain.kicad_pcb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]
2025-09-30 adjusted some freecad files and updated README
    [FinalsTurretTop-Bearing.stl, FinalsTurretTop-Body.stl, FinalsTurretTop-ServoArmFitTest.stl]
2025-10-17 tested servo and pot-meter adc1
    [FinalsTurretTop-Bearing.stl, FinalsTurretTop-LogoStencil.stl, SpeakerStandoffs-Body.stl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]

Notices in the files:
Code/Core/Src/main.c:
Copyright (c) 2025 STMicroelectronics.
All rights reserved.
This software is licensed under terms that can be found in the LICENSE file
